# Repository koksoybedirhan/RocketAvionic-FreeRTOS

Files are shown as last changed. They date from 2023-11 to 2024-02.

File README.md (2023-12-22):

This repository contains the hardware and software of the project named "Orta İrtifa Roketler İçin FreeRTOS Tabanlı STM32 İşlemcili Aviyonik Kart Yazılım Tasarımı", which is entitled to be supported by TÜBİTAK 2209-A.

Main Avionic Components:
<br>
STM32F030C8T6, LORA RA-02, L86-M33 GPS, MPU6050, BMP180
<br>
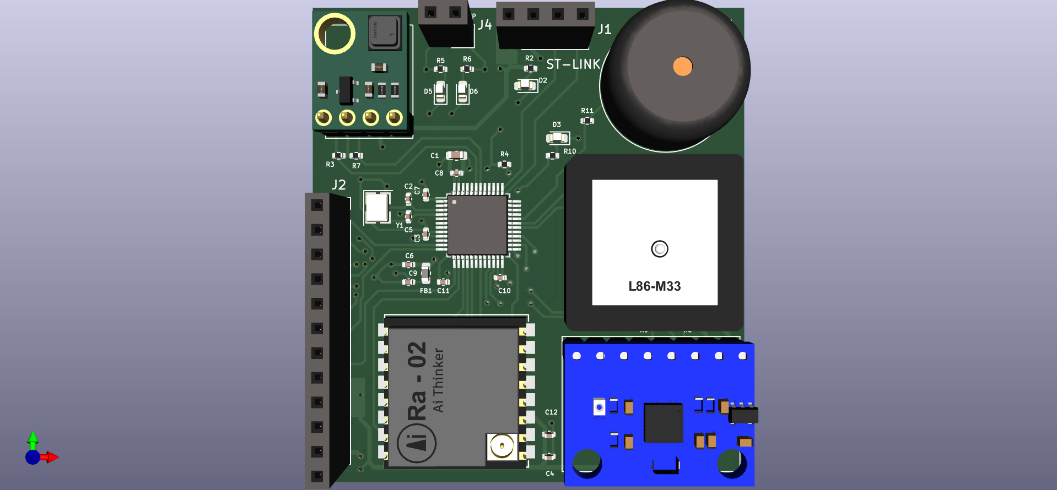
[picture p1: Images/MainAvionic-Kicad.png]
Main Avionic


Ground Station Components:
<br>
STM32F030F4P6, LORA RA-02
<br>
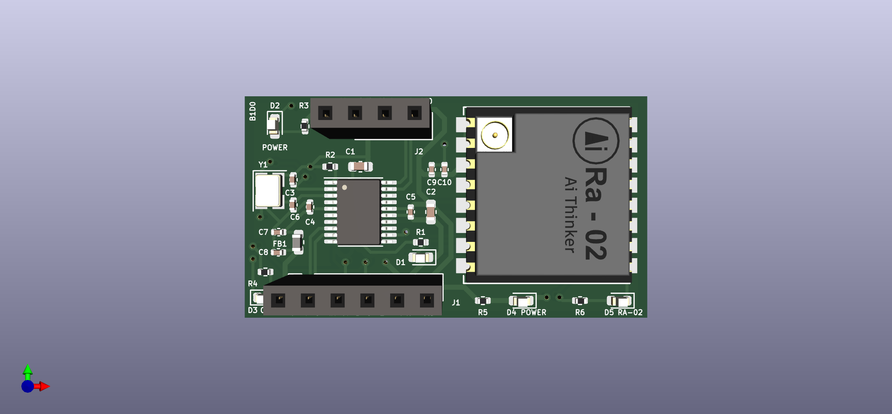
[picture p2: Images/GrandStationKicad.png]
Ground Station


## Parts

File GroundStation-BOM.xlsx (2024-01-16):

Ürün Adı | Birim Fiyatı | Adet | Link
C1, ,"1","100n","C","Capacitor_SMD:C_0603_1608Metric","Unpolarized capacitor","" | 0,16052 ₺ + KDV | 3 | https://ozdisan.com/pasif-komponentler/kapasitorler/smt-smd-ve-mlcc-kapasitorler/CL10B104KB8NNNC/9739
C2, ,"1","10u","C","Capacitor_SMD:C_0603_1608Metric","Unpolarized capacitor","" | 0,41150 ₺ + KDV | 3 | https://ozdisan.com/pasif-komponentler/kapasitorler/smt-smd-ve-mlcc-kapasitorler/CL10A106MQ8NNNC/350721
C3, C6, ,"2","10p","C","Capacitor_SMD:C_0402_1005Metric","Unpolarized capacitor","" | 0,27797 ₺ + KDV | 6 | https://ozdisan.com/pasif-komponentler/kapasitorler/smt-smd-ve-mlcc-kapasitorler/GRT1555C1H100JA02D/859838
C4, ,"1","10n","C","Capacitor_SMD:C_0402_1005Metric","Unpolarized capacitor","" | 0,10179 ₺ + KDV | 3 | https://ozdisan.com/pasif-komponentler/kapasitorler/smt-smd-ve-mlcc-kapasitorler/CL05B103KB5NNNC/30282
C5, ,"1","100n","C","Capacitor_SMD:C_0402_1005Metric","Unpolarized capacitor","" | 0,08222 ₺ + KDV | 3 | https://ozdisan.com/pasif-komponentler/kapasitorler/smt-smd-ve-mlcc-kapasitorler/CL05B104KO5NNNC/336698
C7, C8, ,"2","1u","C","Capacitor_SMD:C_0402_1005Metric","Unpolarized capacitor","" | 0,15269 ₺ + KDV | 6 | https://ozdisan.com/pasif-komponentler/kapasitorler/smt-smd-ve-mlcc-kapasitorler/CC0402KRX5R6BB105/748905
C9, ,"1","22u","C","Capacitor_SMD:C_0402_1005Metric","Unpolarized capacitor","" | 0,20750 ₺ + KDV | 3 | https://ozdisan.com/pasif-komponentler/kapasitorler/smt-smd-ve-mlcc-kapasitorler/CL05A225MQ5NNNC/521876
C10, ,"1","0.1u","C","Capacitor_SMD:C_0402_1005Metric","Unpolarized capacitor","" | 0,08222 ₺ + KDV | 3 | https://ozdisan.com/pasif-komponentler/kapasitorler/smt-smd-ve-mlcc-kapasitorler/CL05B104KO5NNNC/336698
D1, D2, D3, D4, D5, ,"5","LED","LED","LED_SMD:LED_0603_1608Metric","Light emitting diode","" | 1,08386 ₺ + KDV | 18 | https://ozdisan.com/led-ve-aydinlatma-cozumleri/led-komponentler/sinyal-ledler-renkli/19-213USRCS259TR8/645416
FB1, ,"1","120R","FerriteBead","Inductor_SMD:L_0603_1608Metric","Ferrite bead","" | 0,55479 ₺ + KDV | 3 | https://ozdisan.com/pasif-komponentler/induktorler/bead-feritler/LCB1608-101Y-N/487982
J1, ,"1","Conn_01x06_Female","Conn_01x06_Female","Connector_PinSocket_2.54mm:PinSocket_ 1x06_P2.54mm_Vertical","Generic connector, single row, 01x06, script generated (kicad-library-utils/schlib/autogen/connector/)","" | 2,04647 ₺ + KDV | 3 | https://ozdisan.com/konnektor-ve-baglanti-elemanlari/header-konnektorler/disi-headerlar/KLS1-208-1-06-S/457431
J2, ,"1","Conn_01x04_Female","Conn_01x04_Female","Connector_PinSocket_2.54mm:PinSocket_ 1x04_P2.54mm_Vertical","Generic connector, single row, 01x04, script generated (kicad-library-utils/schlib/autogen/connector/)","" | 2,89151 ₺ + KDV | 3 | https://ozdisan.com/konnektor-ve-baglanti-elemanlari/header-konnektorler/disi-headerlar/5PS1SDA85-104G0NNNAL-00/354016
R1, R3, R4, R5, R6, ,"5","330R","R","Resistor_SMD:R_0402_1005Metric","Resistor","" | 0,23099 ₺ + KDV | 15 | https://ozdisan.com/pasif-komponentler/direncler/smt-smd-ve-cip-direncler/CRCW0402330RFKTDBC/712011
R2, ,"1","10K","R","Resistor_SMD:R_0402_1005Metric","Resistor","" | 0,02033 ₺ + KDV | 3 | https://ozdisan.com/pasif-komponentler/direncler/smt-smd-ve-cip-direncler/0402WGJ0103TCE/362331
U1, ,"1","Ai-Thinker-Ra-02","Ai-Thinker-Ra-02","RF_Module:Ai-Thinker-Ra-01-LoRa","Ai-Thinker Ra- 02 410-525 MHz LoRa Module, SPI interface, U.FL antenna connector","" | 274,95 TL | 2 | https://www.robotistan.com/ra02-lora-modulu-antenli
U2, ,"1","STM32F030F4Px","STM32F030F4Px","Package_SO:TSSOP-20_4.4x6.5mm_P0.65mm","ARM Cortex-M0 MCU, 16KB flash, 4KB RAM, 48MHz, 2.4-3.6V, 15 GPIO, TSSOP-20","" | 45,20035 ₺ +KDV | 3 | https://ozdisan.com/entegre-devreler-icler/embedded-entegreler/mikroislemciler/STM32F030F4P6TR/491377
Y1, ,"1","16MHz","Crystal_GND24","Crystal:Crystal_SMD_3225-4Pin_3.2x2.5mm","Four pin crystal, GND on pins 2 and 4","" | 55,54744 ₺ + KDV | 3 | https://ozdisan.com/pasif-komponentler/kristaller-osilatorler-ve-rezanatorler/kristaller/ABM8AIG-25-000MHZ-12-2Z-/630348

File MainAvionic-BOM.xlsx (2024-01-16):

Ürün Adı | Birim Fiyatı | Adet | Link
BZ1, ,"1","Buzzer","Buzzer","Buzzer_Beeper:Buzzer_ 15x7.5RM7.6","Buzzer, polarized","" | 12,54210 ₺ + KDV | 3 | https://ozdisan.com/elektromekanik-komponentler/ses-urunleri/buzzerlar/YX-YT12075-YT03D/483098
C1, ,"1","10u","C","Capacitor_SMD:C_0603_1608Metric","Unpolarized capacitor","" | 0,41189 ₺ + KDV | 3 | https://ozdisan.com/pasif-komponentler/kapasitorler/smt-smd-ve-mlcc-kapasitorler/CL10A106MQ8NNNC/350721
C2, C5, ,"2","10p","C","Capacitor_SMD:C_0402_1005Metric","Unpolarized capacitor","" | 0,27431 ₺ + KDV | 6 | https://ozdisan.com/pasif-komponentler/kapasitorler/smt-smd-ve-mlcc-kapasitorler/GRT1555C1H100JA02D/859838
C3, ,"1","10n","C","Capacitor_SMD:C_0402_1005Metric","Unpolarized capacitor","" | 0,10189 ₺ + KDV | 3 | https://ozdisan.com/pasif-komponentler/kapasitorler/smt-smd-ve-mlcc-kapasitorler/CL05B103KB5NNNC/30282
C4, ,"1","22u","C","Capacitor_SMD:C_0402_1005Metric","Unpolarized capacitor","" | 0,20769 ₺ + KDV | 3 | https://ozdisan.com/pasif-komponentler/kapasitorler/smt-smd-ve-mlcc-kapasitorler/CL05B103KB5NNNC/30282
C6, C9, ,"2","1u","C","Capacitor_SMD:C_0402_1005Metric","Unpolarized capacitor","" | 0,15283 ₺ + KDV | 6 | https://ozdisan.com/pasif-komponentler/kapasitorler/smt-smd-ve-mlcc-kapasitorler/CC0402KRX5R6BB105/748905
C7, C8, C10, C11, ,"4","100n","C","Capacitor_SMD:C_0402_1005Metric","Unpolarized capacitor","" | 0,08229 ₺ + KDV | 12 | https://ozdisan.com/pasif-komponentler/kapasitorler/smt-smd-ve-mlcc-kapasitorler/CL05B104KO5NNNC/336698
C12, ,"1","0.1u","C","Capacitor_SMD:C_0402_1005Metric","Unpolarized capacitor","" | 0,08229 ₺ + KDV | 3 | https://ozdisan.com/pasif-komponentler/kapasitorler/smt-smd-ve-mlcc-kapasitorler/CL05B104KO5NNNC/336698
D2, D3, D5, D6, ,"4","LED","LED","LED_SMD:LED_0603_1608Metric","Light emitting diode","" | 1,08386 ₺ + KDV | 4 | https://ozdisan.com/led-ve-aydinlatma-cozumleri/led-komponentler/sinyal-ledler-renkli/19-213USRCS259TR8/645416
FB1, ,"1","120R","FerriteBead","Inductor_SMD:L_0603_1608Metric","Ferrite bead","" | 0,55479 ₺ + KDV | 3 | https://ozdisan.com/pasif-komponentler/induktorler/bead-feritler/LCB1608-101Y-N/487982
J1, ,"1","Conn_01x04_Female","Conn_01x04_Female","Connector_PinSocket_2.54mm:PinSocket_1x04_P2.54mm_Vertical","Generic connector, single row, 01x04, script generated (kicad-library-utils/schlib/autogen/connector/)","" | 2,89151 ₺ + KDV | 3 | https://ozdisan.com/konnektor-ve-baglanti-elemanlari/header-konnektorler/disi-headerlar/KLS1-208-1-06-S/457431
J2, ,"1","Conn_01x12_Female","Conn_01x12_Female","Connector_PinSocket_2.54mm:PinSocket_1x12_P2.54mm_Vertical","Generic connector, single row, 01x12, script generated (kicad-library-utils/schlib/autogen/connector/)","" | 7,67155 ₺ + KDV | 3 | https://ozdisan.com/konnektor-ve-baglanti-elemanlari/header-konnektorler/disi-headerlar/DS1023-1X12S22/460322
J4, ,"1","Conn_01x02_Female","Conn_01x02_Female","Connector_PinSocket_2.54mm:PinSocket_1x02_P2.54mm_Vertical","Generic connector, single row, 01x02, script generated (kicad-library-utils/schlib/autogen/connector/)","" | 1,57033 ₺ + KDV | 3 | https://ozdisan.com/konnektor-ve-baglanti-elemanlari/header-konnektorler/disi-headerlar/5PS1SDD85-102G0NNNXL-00/450838
R2, R5, R6, R10, ,"4","330R","R","Resistor_SMD:R_0402_1005Metric","Resistor","" | 0,23099 ₺ + KDV | 12 | https://ozdisan.com/pasif-komponentler/direncler/smt-smd-ve-cip-direncler/CRCW0402330RFKTDBC/712011
R3, R7, R8, R9, ,"4","1k5","R","Resistor_SMD:R_0402_1005Metric","Resistor","" | 0,05878 ₺ + KDV | 12 | https://ozdisan.com/pasif-komponentler/direncler/smt-smd-ve-cip-direncler/AC0402FR-071K5L/762346
R4, ,"1","10k","R","Resistor_SMD:R_0402_1005Metric","Resistor","" | 0,02033 ₺ + KDV | 3 | https://ozdisan.com/pasif-komponentler/direncler/smt-smd-ve-cip-direncler/0402WGJ0103TCE/362331
R11, ,"1","100R","R","Resistor_SMD:R_0402_1005Metric","Resistor","" | 0,02035 ₺ + KDV | 3 | https://ozdisan.com/pasif-komponentler/direncler/smt-smd-ve-cip-direncler/0402WGJ0101TCE/443485
U1, ,"1","STM32F030C8Tx","STM32F030C8Tx","Package_QFP:LQFP-48_7x7mm_P0.5mm","ARM Cortex-M0 MCU, 64KB flash, 8KB RAM, 48MHz, 2.4-3.6V, 39 GPIO, LQFP-48","" | 102,93099 ₺ + KDV | 3 | https://ozdisan.com/entegre-devreler-icler/embedded-entegreler/mikroislemciler/STM32F030C8T6/438100
U2, ,"1","Ai-Thinker-Ra-02","Ai-Thinker-Ra-02","RF_Module:Ai-Thinker-Ra-01-LoRa","Ai-Thinker Ra-02 410-525 MHz LoRa Module, SPI interface, U.FL antenna connector","" | 274,95 TL | 4 | https://www.robotistan.com/ra02-lora-modulu-antenli
U3, ,"1","L86-M33","L86-M33","F030C8T6:L86-M33","","" | 361,19 TL | 3 | https://www.empastore.com/l86-m33?gad_source=1
U4, ,"1","MPU6050","MPU6050","F030C8T6:MPU6050","","" | 77,72 TL | 3 | https://www.robotistan.com/mpu6050-6-eksen-ivme-ve-gyro-sensoru-6-dof-3-axis-accelerometer-and-gyros
U5, ,"1","BMP180","BMP180","F030C8T6:BMP180","","" | 24,45 TL | 3 | https://www.direnc.net/bmp180-dijital-barometrik-sensor
Y1, ,"1","16MHz","Crystal_GND24","Crystal:Crystal_SMD_3225-4Pin_3.2x2.5mm","Four pin crystal, GND on pins 2 and 4","" | 55,54744 ₺ + KDV | 3 | https://ozdisan.com/pasif-komponentler/kristaller-osilatorler-ve-rezanatorler/kristaller/ABM8AIG-25-000MHZ-12-2Z-/630348

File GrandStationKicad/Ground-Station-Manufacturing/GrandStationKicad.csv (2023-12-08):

Source: | C:\Users\Lenovo\Desktop\Bedirhan\TUBITAK\RocketAvionic-FreeRTOS\GrandStationKicad\GrandStationKicad.kicad_sch
Date: | Sat Dec 9 00:15:10 2023
Tool: | Eeschema (6.0.6)
Generator: | C:\Program Files\KiCad\6.0\bin\scripting\plugins/bom_csv_grouped_by_value_with_fp.py
Component Count: | 27
Ref | Qnty | Value | Cmp name | Footprint | Description | Vendor
C1, | 1 | 100n | C | Capacitor_SMD:C_0603_1608Metric | Unpolarized capacitor
C2, | 1 | 10u | C | Capacitor_SMD:C_0603_1608Metric | Unpolarized capacitor
C3, C6, | 2 | 10p | C | Capacitor_SMD:C_0402_1005Metric | Unpolarized capacitor
C4, | 1 | 10n | C | Capacitor_SMD:C_0402_1005Metric | Unpolarized capacitor
C5, | 1 | 100n | C | Capacitor_SMD:C_0402_1005Metric | Unpolarized capacitor
C7, C8, | 2 | 1u | C | Capacitor_SMD:C_0402_1005Metric | Unpolarized capacitor
C9, | 1 | 22u | C | Capacitor_SMD:C_0402_1005Metric | Unpolarized capacitor
C10, | 1 | 0.1u | C | Capacitor_SMD:C_0402_1005Metric | Unpolarized capacitor
D1, D2, D3, D4, D5, | 5 | LED | LED | LED_SMD:LED_0603_1608Metric | Light emitting diode
FB1, | 1 | 120R | FerriteBead | Inductor_SMD:L_0603_1608Metric | Ferrite bead
J1, | 1 | Conn_01x06_Female | Conn_01x06_Female | Connector_PinSocket_2.54mm:PinSocket_1x06_P2.54mm_Vertical | Generic connector, single row, 01x06, script generated (kicad-library-utils/schlib/autogen/connector/)
J2, | 1 | Conn_01x04_Female | Conn_01x04_Female | Connector_PinSocket_2.54mm:PinSocket_1x04_P2.54mm_Vertical | Generic connector, single row, 01x04, script generated (kicad-library-utils/schlib/autogen/connector/)
R1, R3, R4, R5, R6, | 5 | 330R | R | Resistor_SMD:R_0402_1005Metric | Resistor
R2, | 1 | R | R | Resistor_SMD:R_0402_1005Metric | Resistor
U1, | 1 | Ai-Thinker-Ra-02 | Ai-Thinker-Ra-02 | RF_Module:Ai-Thinker-Ra-01-LoRa | Ai-Thinker Ra-02 410-525 MHz LoRa Module, SPI interface, U.FL antenna connector
U2, | 1 | STM32F030F4Px | STM32F030F4Px | Package_SO:TSSOP-20_4.4x6.5mm_P0.65mm | ARM Cortex-M0 MCU, 16KB flash, 4KB RAM, 48MHz, 2.4-3.6V, 15 GPIO, TSSOP-20
Y1, | 1 | 16MHz | Crystal_GND24 | Crystal:Crystal_SMD_3225-4Pin_3.2x2.5mm | Four pin crystal, GND on pins 2 and 4

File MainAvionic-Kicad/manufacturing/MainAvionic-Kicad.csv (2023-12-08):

Source: | C:\Users\Lenovo\Desktop\Bedirhan\TUBITAK\RocketAvionic-FreeRTOS\MainAvionic-Kicad\MainAvionic-Kicad.kicad_sch
Date: | Sat Dec 9 00:03:14 2023
Tool: | Eeschema (6.0.6)
Generator: | C:\Program Files\KiCad\6.0\bin\scripting\plugins/bom_csv_grouped_by_value_with_fp.py
Component Count: | 37
Ref | Qnty | Value | Cmp name | Footprint | Description | Vendor
BZ1, | 1 | Buzzer | Buzzer | Buzzer_Beeper:Buzzer_15x7.5RM7.6 | Buzzer, polarized
C1, | 1 | 10u | C | Capacitor_SMD:C_0603_1608Metric | Unpolarized capacitor
C2, C5, | 2 | 10p | C | Capacitor_SMD:C_0402_1005Metric | Unpolarized capacitor
C3, | 1 | 10n | C | Capacitor_SMD:C_0402_1005Metric | Unpolarized capacitor
C4, | 1 | 22u | C | Capacitor_SMD:C_0402_1005Metric | Unpolarized capacitor
C6, C9, | 2 | 1u | C | Capacitor_SMD:C_0402_1005Metric | Unpolarized capacitor
C7, C8, C10, C11, | 4 | 100n | C | Capacitor_SMD:C_0402_1005Metric | Unpolarized capacitor
C12, | 1 | 0.1u | C | Capacitor_SMD:C_0402_1005Metric | Unpolarized capacitor
D2, D3, D5, D6, | 4 | LED | LED | LED_SMD:LED_0603_1608Metric | Light emitting diode
FB1, | 1 | 120R | FerriteBead | Inductor_SMD:L_0603_1608Metric | Ferrite bead
J1, | 1 | Conn_01x04_Female | Conn_01x04_Female | Connector_PinSocket_2.54mm:PinSocket_1x04_P2.54mm_Vertical | Generic connector, single row, 01x04, script generated (kicad-library-utils/schlib/autogen/connector/)
J2, | 1 | Conn_01x12_Female | Conn_01x12_Female | Connector_PinSocket_2.54mm:PinSocket_1x12_P2.54mm_Vertical | Generic connector, single row, 01x12, script generated (kicad-library-utils/schlib/autogen/connector/)
J4, | 1 | Conn_01x02_Female | Conn_01x02_Female | Connector_PinSocket_2.54mm:PinSocket_1x02_P2.54mm_Vertical | Generic connector, single row, 01x02, script generated (kicad-library-utils/schlib/autogen/connector/)
R2, R5, R6, R10, | 4 | 330R | R | Resistor_SMD:R_0402_1005Metric | Resistor
R3, R7, R8, R9, | 4 | 1k5 | R | Resistor_SMD:R_0402_1005Metric | Resistor
R4, | 1 | 10k | R | Resistor_SMD:R_0402_1005Metric | Resistor
R11, | 1 | 100R | R | Resistor_SMD:R_0402_1005Metric | Resistor
U1, | 1 | STM32F030C8Tx | STM32F030C8Tx | Package_QFP:LQFP-48_7x7mm_P0.5mm | ARM Cortex-M0 MCU, 64KB flash, 8KB RAM, 48MHz, 2.4-3.6V, 39 GPIO, LQFP-48
U2, | 1 | Ai-Thinker-Ra-02 | Ai-Thinker-Ra-02 | RF_Module:Ai-Thinker-Ra-01-LoRa | Ai-Thinker Ra-02 410-525 MHz LoRa Module, SPI interface, U.FL antenna connector
U3, | 1 | L86-M33 | L86-M33 | F030C8T6:L86-M33
U4, | 1 | MPU6050 | MPU6050 | F030C8T6:MPU6050
U5, | 1 | BMP180 | BMP180 | F030C8T6:BMP180
Y1, | 1 | 16MHz | Crystal_GND24 | Crystal:Crystal_SMD_3225-4Pin_3.2x2.5mm | Four pin crystal, GND on pins 2 and 4

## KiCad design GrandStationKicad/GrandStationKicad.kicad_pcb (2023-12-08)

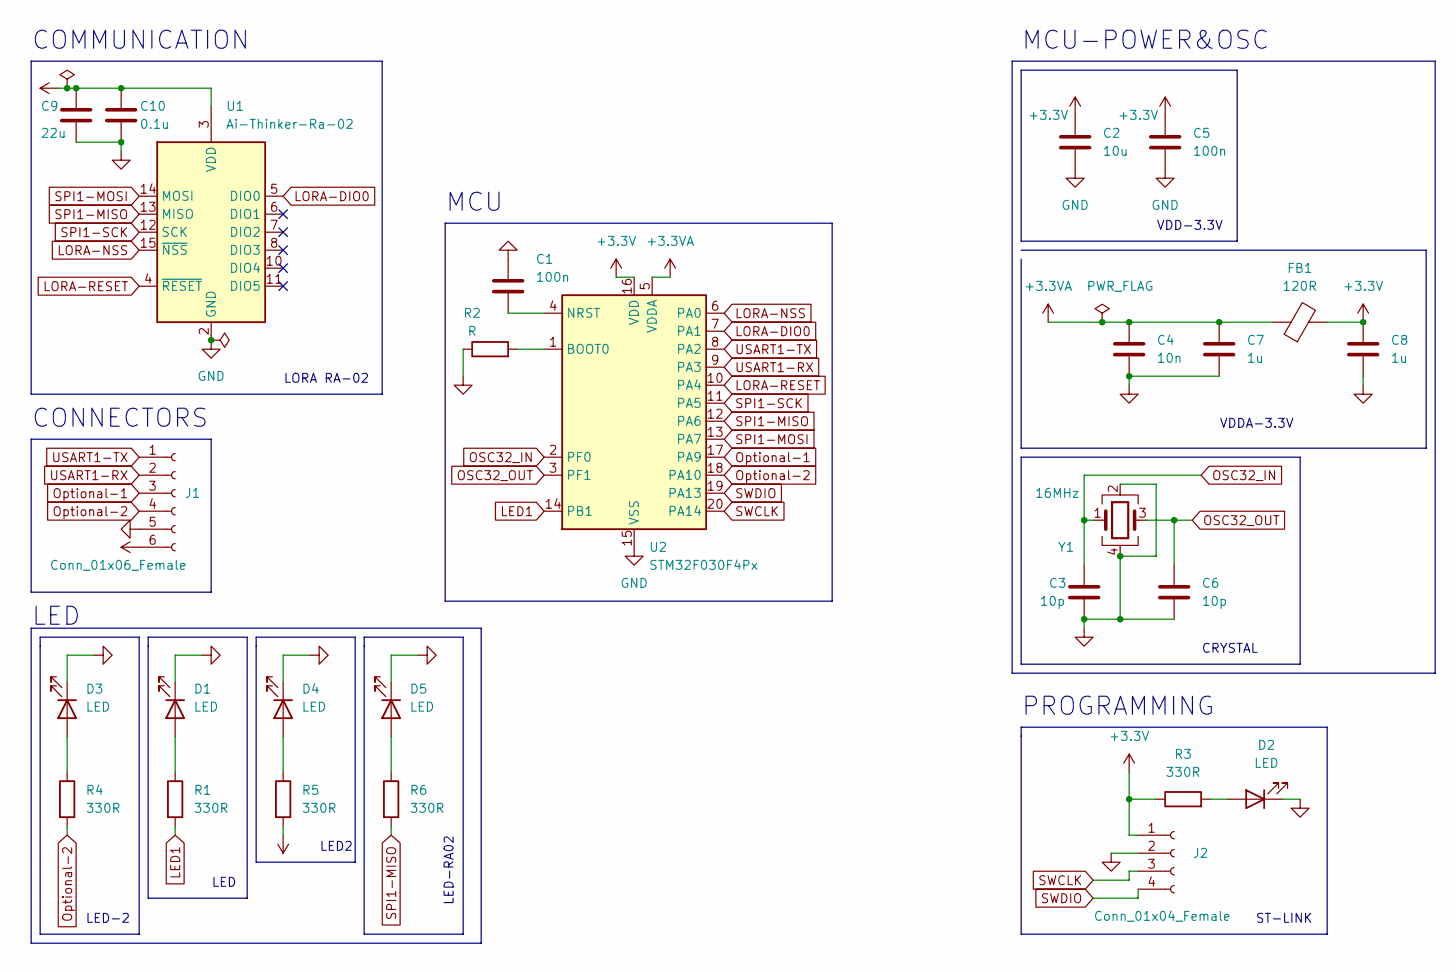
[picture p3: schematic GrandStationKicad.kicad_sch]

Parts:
C1: 100n; C_0603_1608Metric
C2: 10u; C_0603_1608Metric
C3, C6: 10p; C_0402_1005Metric
C4: 10n; C_0402_1005Metric
C5: 100n; C_0402_1005Metric
C7, C8: 1u; C_0402_1005Metric
C9: 22u; C_0402_1005Metric
C10: 0.1u; C_0402_1005Metric
D1, D2, D3, D4, D5: LED; LED_0603_1608Metric
FB1: 120R; L_0603_1608Metric
J1: Conn_01x06_Female; PinSocket_1x06_P2.54mm_Vertical
J2: Conn_01x04_Female; PinSocket_1x04_P2.54mm_Vertical
R1, R3, R4, R5, R6: 330R; R_0402_1005Metric
R2: R; R_0402_1005Metric
U1: Ai-Thinker-Ra-02; Ai-Thinker-Ra-01-LoRa
U2: STM32F030F4Px; TSSOP-20_4.4x6.5mm_P0.65mm
Y1: 16MHz; Crystal_SMD_3225-4Pin_3.2x2.5mm

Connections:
+3.3V: C2.1, C5.1, C8.1, C9.1, C10.1, FB1.2, J1.6, J2.1, R3.1, R5.2, U1.3 (VDD), U2.16 (VDD)
+3.3VA: C4.1, C7.1, FB1.1, U2.5 (VDDA)
GND: C1.1, C2.2, C3.2, C4.2, C5.2, C6.2, C7.2, C8.2, C9.2, C10.2, D1.1 (K), D2.1 (K), D3.1 (K), D4.1 (K), D5.1 (K), J1.5, J2.2, R2.1, U1.1 (GND), U1.2 (GND), U1.9 (GND), U1.16 (GND), U2.15 (VSS), Y1.2, Y1.4
LED1: R1.2, U2.14 (PB1)
LORA-DIO0: U1.5 (DIO0), U2.7 (PA1)
LORA-NSS: U1.15 (~NSS), U2.6 (PA0)
LORA-RESET: U1.4 (~RESET), U2.10 (PA4)
unnamed: C1.2, U2.4 (NRST)
unnamed: D1.2 (A), R1.1
unnamed: D2.2 (A), R3.2
unnamed: D3.2 (A), R4.1
unnamed: D4.2 (A), R5.1
unnamed: D5.2 (A), R6.1
unnamed: R2.2, U2.1 (BOOT0)
OSC32_IN: C3.1, U2.2 (PF0), Y1.1
OSC32_OUT: C6.1, U2.3 (PF1), Y1.3
Optional-1: J1.3, U2.17 (PA9)
Optional-2: J1.4, R4.2, U2.18 (PA10)
SPI1-MISO: R6.2, U1.13 (MISO), U2.12 (PA6)
SPI1-MOSI: U1.14 (MOSI), U2.13 (PA7)
SPI1-SCK: U1.12 (SCK), U2.11 (PA5)
SWCLK: J2.3, U2.20 (PA14)
SWDIO: J2.4, U2.19 (PA13)
USART1-RX: J1.2, U2.9 (PA3)
USART1-TX: J1.1, U2.8 (PA2)

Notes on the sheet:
MCU
LED
COMMUNICATION
VDDA-3.3V
PROGRAMMING
LED-RA02
CONNECTORS
LED-2
LED
VDD-3.3V
CRYSTAL
MCU-POWER&OSC
LORA RA-02
LED2
ST-LINK

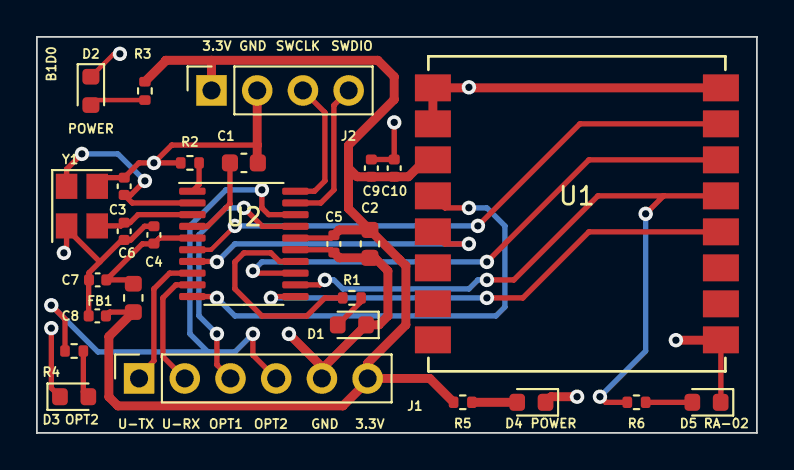
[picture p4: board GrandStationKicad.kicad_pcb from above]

Board: 2 copper layers, 40.0 x 22.0 mm, 27 parts (0 on the bottom side), 25 nets.

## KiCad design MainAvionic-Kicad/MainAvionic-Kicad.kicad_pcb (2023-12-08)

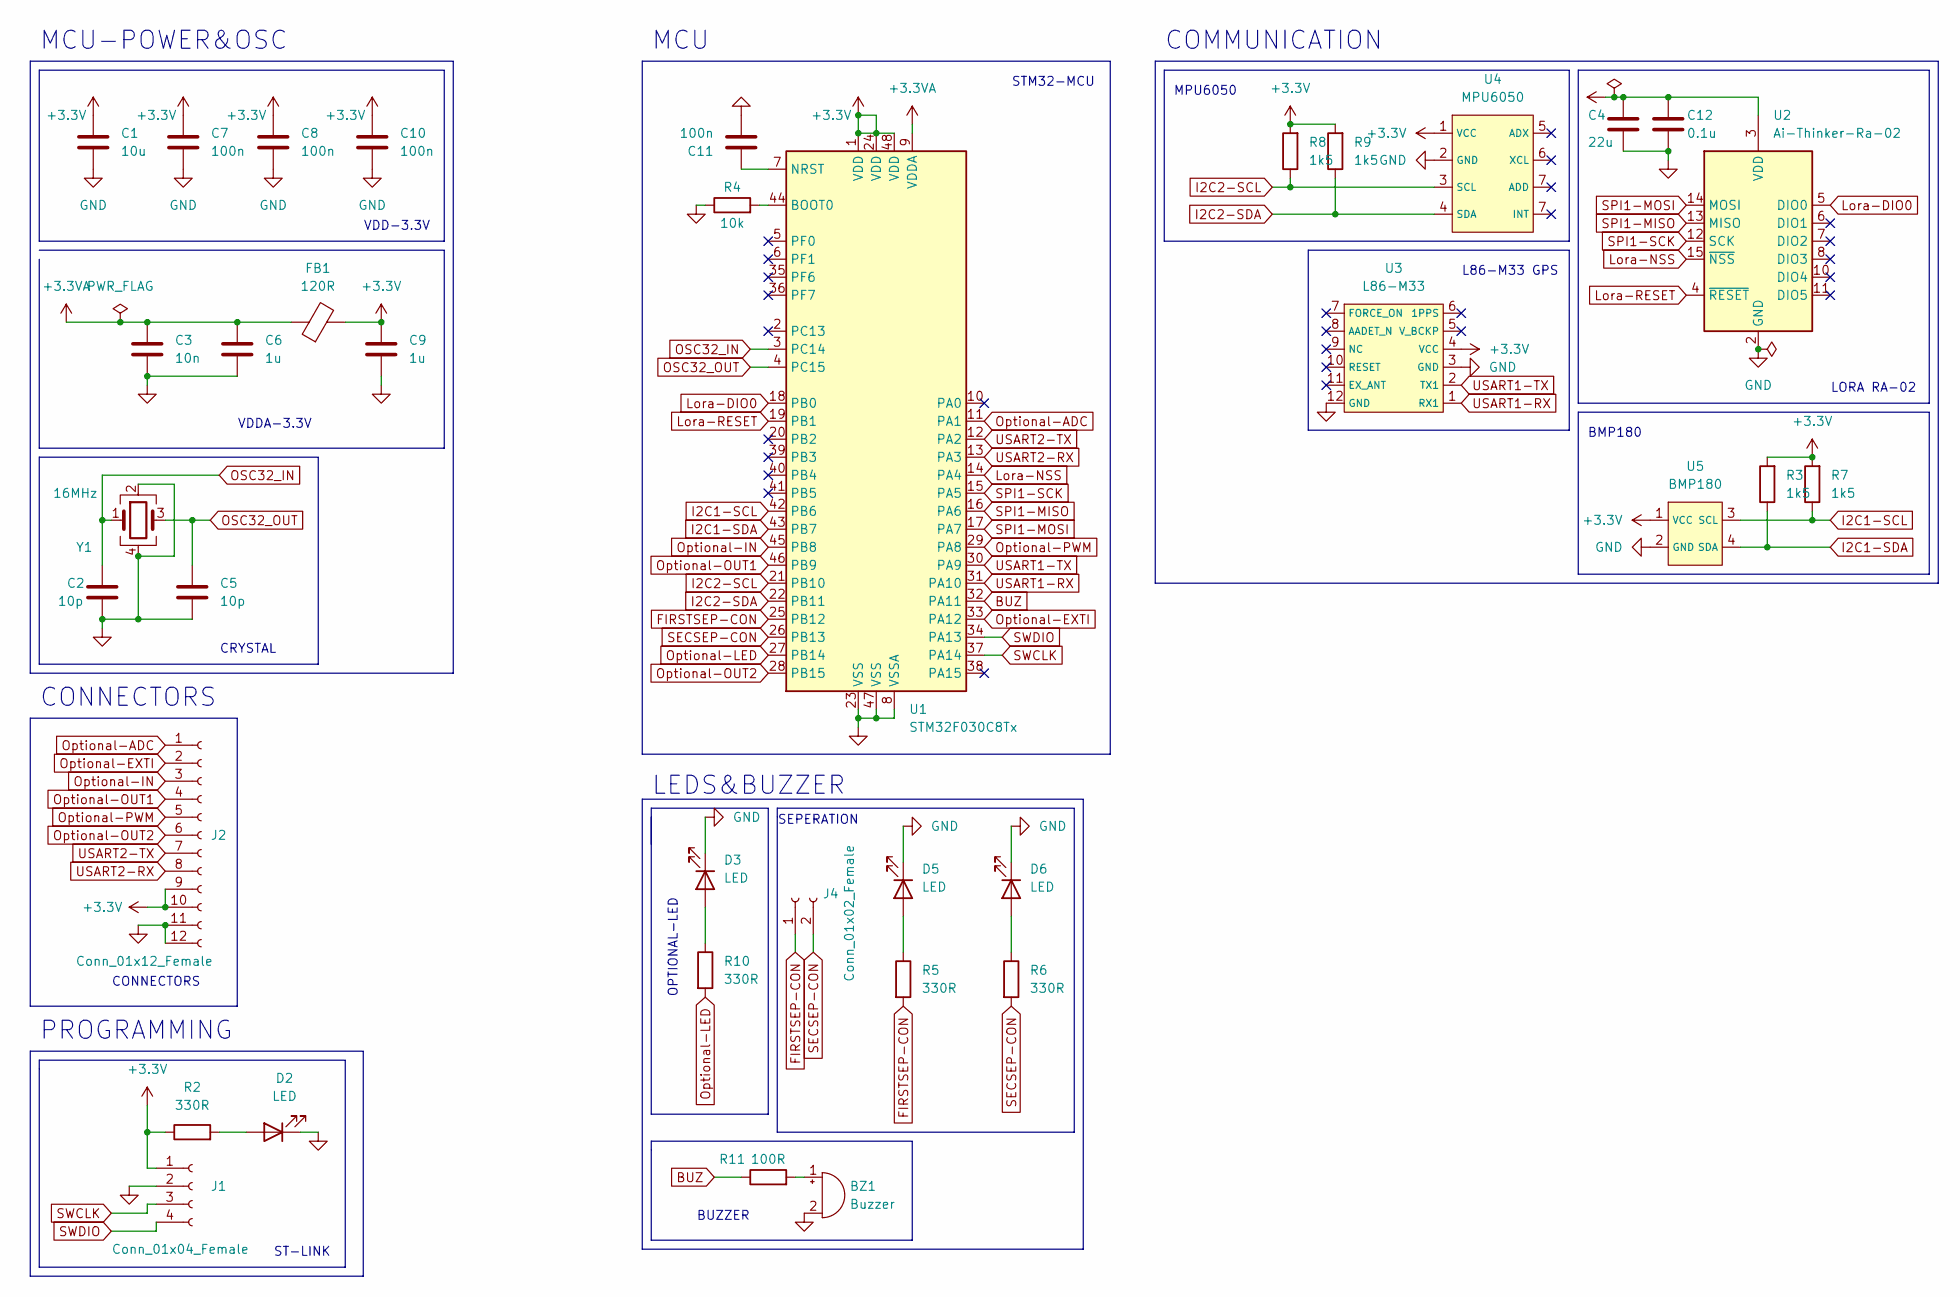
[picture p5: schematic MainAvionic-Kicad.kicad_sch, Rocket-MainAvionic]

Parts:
BZ1: Buzzer; Buzzer_15x7.5RM7.6
C1: 10u; C_0603_1608Metric
C2, C5: 10p; C_0402_1005Metric
C3: 10n; C_0402_1005Metric
C4: 22u; C_0402_1005Metric
C6, C9: 1u; C_0402_1005Metric
C7, C8, C10, C11: 100n; C_0402_1005Metric
C12: 0.1u; C_0402_1005Metric
D2, D3, D5, D6: LED; LED_0603_1608Metric
FB1: 120R; L_0603_1608Metric
J1: Conn_01x04_Female; PinSocket_1x04_P2.54mm_Vertical
J2: Conn_01x12_Female; PinSocket_1x12_P2.54mm_Vertical
J4: Conn_01x02_Female; PinSocket_1x02_P2.54mm_Vertical
R2, R5, R6, R10: 330R; R_0402_1005Metric
R3, R7, R8, R9: 1k5; R_0402_1005Metric
R4: 10k; R_0402_1005Metric
R11: 100R; R_0402_1005Metric
U1: STM32F030C8Tx; LQFP-48_7x7mm_P0.5mm
U2: Ai-Thinker-Ra-02; Ai-Thinker-Ra-01-LoRa
U3: L86-M33
U4: MPU6050
U5: BMP180
Y1: 16MHz; Crystal_SMD_3225-4Pin_3.2x2.5mm

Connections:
+3.3V: C1.1, C4.1, C7.1, C8.1, C9.1, C10.1, C12.1, FB1.2, J1.1, J2.9, J2.10, R2.1, R3.2, R7.2, R8.2, R9.2, U1.1 (VDD), U1.24 (VDD), U1.48 (VDD), U2.3 (VDD), U3.4 (VCC), U4.1 (VCC), U5.1 (VCC)
+3.3VA: C3.1, C6.1, FB1.1, U1.9 (VDDA)
BUZ: R11.1, U1.32 (PA11)
FIRSTSEP-CON: J4.1, R5.2, U1.25 (PB12)
GND: BZ1.2 (+), C1.2, C2.2, C3.2, C4.2, C5.2, C6.2, C7.2, C8.2, C9.2, C10.2, C11.2, C12.2, D2.1 (K), D3.1 (K), D5.1 (K), D6.1 (K), J1.2, J2.11, J2.12, R4.1, U1.8 (VSSA), U1.23 (VSS), U1.47 (VSS), U2.1 (GND), U2.2 (GND), U2.9 (GND), U2.16 (GND), U3.3 (GND), U3.12 (GND), U4.2 (GND), U5.2 (GND), Y1.2, Y1.4
I2C1-SCL: R7.1, U1.42 (PB6), U5.3 (SCL)
I2C1-SDA: R3.1, U1.43 (PB7), U5.4 (SDA)
I2C2-SCL: R8.1, U1.21 (PB10), U4.3 (SCL)
I2C2-SDA: R9.1, U1.22 (PB11), U4.4 (SDA)
Lora-DIO0: U1.18 (PB0), U2.5 (DIO0)
Lora-NSS: U1.14 (PA4), U2.15 (~NSS)
Lora-RESET: U1.19 (PB1), U2.4 (~RESET)
unnamed: BZ1.1 (-), R11.2
unnamed: C11.1, U1.7 (NRST)
unnamed: D2.2 (A), R2.2
unnamed: D3.2 (A), R10.1
unnamed: D5.2 (A), R5.1
unnamed: D6.2 (A), R6.1
unnamed: R4.2, U1.44 (BOOT0)
OSC32_IN: C2.1, U1.3 (PC14), Y1.1
OSC32_OUT: C5.1, U1.4 (PC15), Y1.3
Optional-ADC: J2.1, U1.11 (PA1)
Optional-EXTI: J2.2, U1.33 (PA12)
Optional-IN: J2.3, U1.45 (PB8)
Optional-LED: R10.2, U1.27 (PB14)
Optional-OUT1: J2.4, U1.46 (PB9)
Optional-OUT2: J2.6, U1.28 (PB15)
Optional-PWM: J2.5, U1.29 (PA8)
SECSEP-CON: J4.2, R6.2, U1.26 (PB13)
SPI1-MISO: U1.16 (PA6), U2.13 (MISO)
SPI1-MOSI: U1.17 (PA7), U2.14 (MOSI)
SPI1-SCK: U1.15 (PA5), U2.12 (SCK)
SWCLK: J1.3, U1.37 (PA14)
SWDIO: J1.4, U1.34 (PA13)
USART1-RX: U1.31 (PA10), U3.1 (RX1)
USART1-TX: U1.30 (PA9), U3.2 (TX1)
USART2-RX: J2.8, U1.13 (PA3)
USART2-TX: J2.7, U1.12 (PA2)

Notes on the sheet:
VDD-3.3V
STM32-MCU
LEDS&BUZZER
BUZZER
PROGRAMMING
MCU-POWER&OSC
VDDA-3.3V
CONNECTORS
CONNECTORS
COMMUNICATION
CRYSTAL
MCU
ST-LINK
SEPERATION
LORA RA-02
BMP180
MPU6050
L86-M33 GPS
OPTIONAL-LED

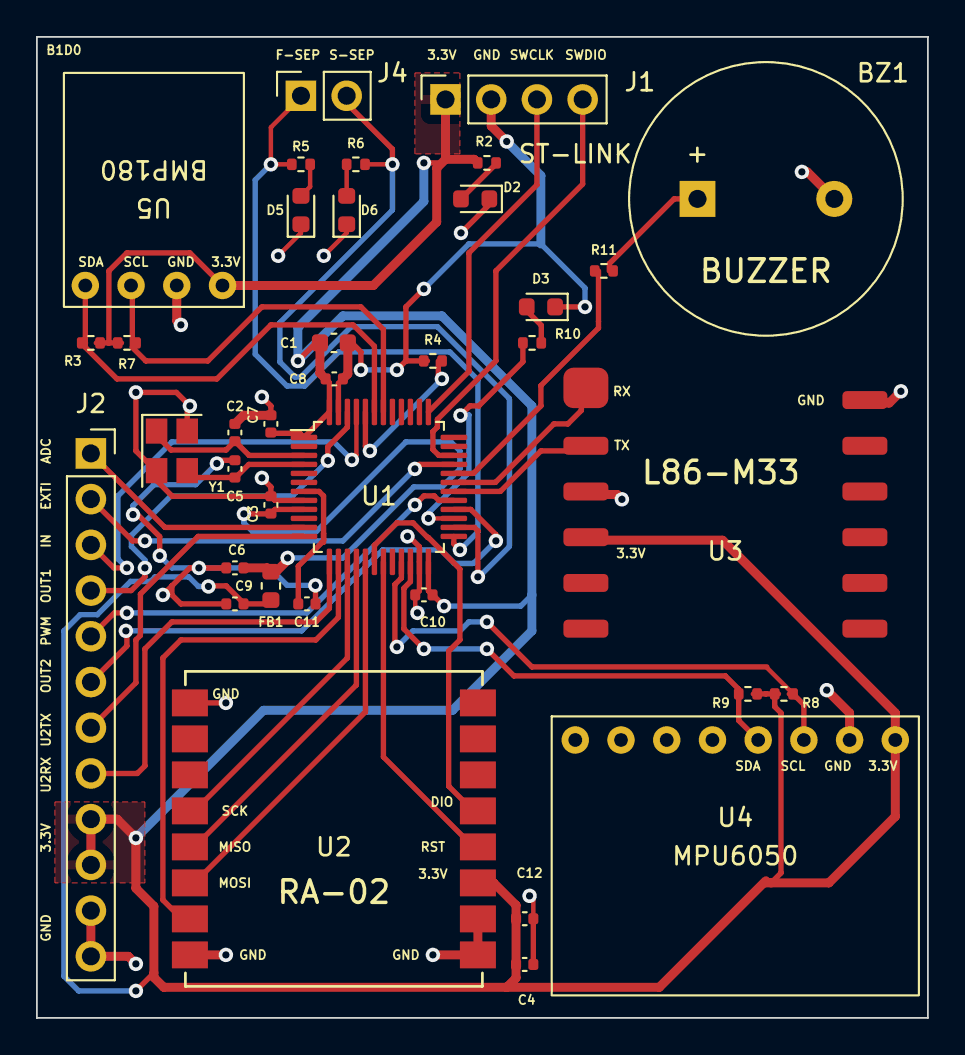
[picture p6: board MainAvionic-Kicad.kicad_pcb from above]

Board: 2 copper layers, 49.5 x 54.5 mm, 37 parts (0 on the bottom side), 38 nets.

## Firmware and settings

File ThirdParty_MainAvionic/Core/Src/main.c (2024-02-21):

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
/* Includes ------------------------------------------------------------------*/
#include "main.h"
#include "cmsis_os.h"

/* USER CODE BEGIN Includes */
#include"lwgps/lwgps.h"
#include "bme280.h"
#include "mpu6050.h"
//#include "mpu6050.c"

#include <math.h>
/* USER CODE END Includes */

I2C_HandleTypeDef hi2c1;

TIM_HandleTypeDef htim1;

UART_HandleTypeDef huart2;
UART_HandleTypeDef huart6;

osThreadId defaultTaskHandle;
osThreadId SeperationTaskHandle;
osThreadId SepSensorTaskHandle;
osThreadId GPSTaskHandle;
osThreadId CommTaskHandle;
osMutexId SimpleMutexHandle;
osSemaphoreId BinSemSepHandle;
void SystemClock_Config(void);
static void MX_GPIO_Init(void);
static void MX_I2C1_Init(void);
static void MX_USART6_UART_Init(void);
static void MX_USART2_UART_Init(void);
static void MX_TIM1_Init(void);
void StartDefaultTask(void const *argument);
void StartSeperationTask(void const *argument);
void StartSepSensorTask(void const *argument);
void StartGPSTask(void const *argument);
void StartCommTask(void const *argument);

/* USER CODE BEGIN 0 */
#define BUFFER_SIZE 25
float sensorValues[BUFFER_SIZE];
float RollAng, Altitude1, Temperature, Pressure, Humidity;
float acX, acY, acZ, gyX, gyY, gyZ, Alt, T, P, H, AltCompare;
float gpsAlt, gpsLat, gpsLong;
unsigned char buff[54];
int flag = 1;
int flagDown = 0;
int sayac = 0;
int deneme;

lwgps_t gps;
uint8_t rx_buffer[128];
uint8_t rx_index = 0;
uint8_t rx_data = 0;

typedef union {
	float sayi;
	unsigned char array[4];
} float32toInt8;

void HAL_UART_RxCpltCallback(UART_HandleTypeDef *huart) {
	if (huart == &huart6) {
		if (rx_data != '\n' && rx_index < sizeof(rx_buffer)) {
			rx_buffer[rx_index++] = rx_data;
		} else {
			lwgps_process(&gps, rx_buffer, rx_index + 1);
			rx_index = 0;
			rx_data = 0;
		}
		HAL_UART_Receive_IT(&huart6, &rx_data, 1);
	}
}

//roketin aşağı gittiği anlayan verilerin doldurulduğu buffer'i sıfırlayan kod.
void initSensorBuffer() {
	for (int i = 0; i < BUFFER_SIZE; i++) {
		sensorValues[i] = 0.0f;
	}
}

//roketin aşağı indiğini anlayan kod (buffer'a veri atıp karşılaştırma yapıyor)
void processSensorValues() {
	for (int i = 0; i < BUFFER_SIZE; i += 4) {
		if (i + 24 < BUFFER_SIZE) {
			if (sensorValues[i] >= sensorValues[i + 24]) {
				flagDown = 1;
			} else {
				flagDown = 0;
			}
		}

		// Buffer'ı sıfırla
		if (i == BUFFER_SIZE - 4) {
			initSensorBuffer();
		}
	}
}

unsigned char cs() {
	int checkSum = 0;
	for (int i = 4; i < 51; i++) {
		checkSum += buff[i];
	}
	return (unsigned char) (checkSum % 256);
}

void paket(int sayac) {
	buff[0] = 0xFF; //sabit
	buff[1] = 0xFF; //sabit
	buff[2] = 0x54; //sabit
	buff[3] = 0x52; //sabit
	buff[4] = 0x01; //id = 1 kabul ettik
	buff[5] = sayac; //paket sayaci

	float32toInt8 alt_donusturme;
	alt_donusturme.sayi = Alt;
	buff[6] = alt_donusturme.array[0];
	buff[7] = alt_donusturme.array[1];
	buff[8] = alt_donusturme.array[2];
	buff[9] = alt_donusturme.array[3];

	float32toInt8 gpsAltDonusturme;
	gpsAltDonusturme.sayi = gpsAlt;
	buff[10] = gpsAltDonusturme.array[0];
	buff[11] = gpsAltDonusturme.array[1];
	buff[12] = gpsAltDonusturme.array[2];
	buff[13] = gpsAltDonusturme.array[3];

	float32toInt8 gpsLatDonusturme;
	gpsLatDonusturme.sayi = gpsLat;
	buff[14] = gpsLatDonusturme.array[0];
	buff[15] = gpsLatDonusturme.array[1];
	buff[16] = gpsLatDonusturme.array[2];
	buff[17] = gpsLatDonusturme.array[3];

	float32toInt8 gpsLongDonusturme;
	gpsLongDonusturme.sayi = gpsLong;
	buff[18] = gpsLongDonusturme.array[0];
	buff[19] = gpsLongDonusturme.array[1];
	buff[20] = gpsLongDonusturme.array[2];
	buff[21] = gpsLongDonusturme.array[3];

	float32toInt8 AccX;
	AccX.sayi = acX;
	buff[22] = AccX.array[0];
	buff[23] = AccX.array[1];
	buff[24] = AccX.array[2];
	buff[25] = AccX.array[3];

	float32toInt8 AccY;
	AccY.sayi = acY;
	buff[26] = AccY.array[0];
	buff[27] = AccY.array[1];
	buff[28] = AccY.array[2];
	buff[29] = AccY.array[3];

	float32toInt8 AccZ;
	AccZ.sayi = acZ;
	buff[30] = AccZ.array[0];
	buff[31] = AccZ.array[1];
	buff[32] = AccZ.array[2];
	buff[33] = AccZ.array[3];

	float32toInt8 GyroX;
	GyroX.sayi = gyX;
	buff[34] = GyroX.array[0];
	buff[35] = GyroX.array[1];
	buff[36] = GyroX.array[2];
	buff[37] = GyroX.array[3];

	float32toInt8 GyroY;
	GyroY.sayi = gyY;
	buff[38] = GyroY.array[0];
	buff[39] = GyroY.array[1];
	buff[40] = GyroY.array[2];
	buff[41] = GyroY.array[3];

	float32toInt8 GyroZ;
	GyroZ.sayi = gyZ;
	buff[42] = GyroZ.array[0];
	buff[43] = GyroZ.array[1];
	buff[44] = GyroZ.array[2];
	buff[45] = GyroZ.array[3];

	float32toInt8 Aci;
	Aci.sayi = RollAng;
	buff[46] = Aci.array[0];
	buff[47] = Aci.array[1];
	buff[48] = Aci.array[2];
	buff[49] = Aci.array[3];

	buff[50] = flag; //durum
	buff[51] = cs(); //check-sum
	buff[52] = 0x0D; //sabit
	buff[53] = 0x0A; //sabit
}

/* USER CODE END 0 */

/**
 * @brief  The application entry point.
 * @retval int
 */
int main(void) {
	/* MCU Configuration--------------------------------------------------------*/

	/* Reset of all peripherals, Initializes the Flash interface and the Systick. */
	HAL_Init();

	/* Configure the system clock */
	SystemClock_Config();

	/* Initialize all configured peripherals */
	MX_GPIO_Init();
	MX_I2C1_Init();
	MX_USART6_UART_Init();
	MX_USART2_UART_Init();
	MX_TIM1_Init();
	/* USER CODE BEGIN 2 */

	HAL_TIM_Base_Init(&htim1);
	MPU6050_Init();
	lwgps_init(&gps);
	HAL_UART_Receive_IT(&huart6, &rx_data, 1);
	BME280_Config(OSRS_2, OSRS_16, OSRS_1, MODE_NORMAL, T_SB_0p5, IIR_16);

	/* USER CODE END 2 */

	/* Create the mutex(es) */
	/* definition and creation of SimpleMutex */
	osMutexDef(SimpleMutex);
	SimpleMutexHandle = osMutexCreate(osMutex(SimpleMutex));

	/* USER CODE BEGIN RTOS_MUTEX */
	/* add mutexes, ... */
	/* USER CODE END RTOS_MUTEX */

	/* Create the semaphores(s) */
	/* definition and creation of BinSemSep */
	osSemaphoreDef(BinSemSep);
	BinSemSepHandle = osSemaphoreCreate(osSemaphore(BinSemSep), 1);

	/* USER CODE BEGIN RTOS_SEMAPHORES */
	/* add semaphores, ... */
	/* USER CODE END RTOS_SEMAPHORES */

	/* USER CODE BEGIN RTOS_TIMERS */
	/* start timers, add new ones, ... */
	/* USER CODE END RTOS_TIMERS */

	/* USER CODE BEGIN RTOS_QUEUES */
	/* add queues, ... */
	/* USER CODE END RTOS_QUEUES */

	/* Create the thread(s) */
	/* definition and creation of defaultTask */
	osThreadDef(defaultTask, StartDefaultTask, osPriorityIdle, 0, 128);
	defaultTaskHandle = osThreadCreate(osThread(defaultTask), NULL);

	/* definition and creation of SeperationTask */
	osThreadDef(SeperationTask, StartSeperationTask, osPriorityAboveNormal, 0,
			128);
	SeperationTaskHandle = osThreadCreate(osThread(SeperationTask), NULL);

	/* definition and creation of SepSensorTask */
	osThreadDef(SepSensorTask, StartSepSensorTask, osPriorityNormal, 0, 128);
	SepSensorTaskHandle = osThreadCreate(osThread(SepSensorTask), NULL);

	/* definition and creation of GPSTask */
	osThreadDef(GPSTask, StartGPSTask, osPriorityBelowNormal, 0, 128);
	GPSTaskHandle = osThreadCreate(osThread(GPSTask), NULL);

	/* definition and creation of CommTask */
	osThreadDef(CommTask, StartCommTask, osPriorityLow, 0, 128);
	CommTaskHandle = osThreadCreate(osThread(CommTask), NULL);

	/* USER CODE BEGIN RTOS_THREADS */
	/* add threads, ... */
	/* USER CODE END RTOS_THREADS */

	/* Start scheduler */
	osKernelStart();

	/* We should never get here as control is now taken by the scheduler */
	/* Infinite loop */
	/* USER CODE BEGIN WHILE */
	while (1) {
		/* USER CODE END WHILE */

		/* USER CODE BEGIN 3 */
	}
	/* USER CODE END 3 */
}

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
/* USER CODE BEGIN Header_StartDefaultTask */
/**
 * @brief  Function implementing the defaultTask thread.
 * @param  argument: Not used
 * @retval None
 */
/* USER CODE END Header_StartDefaultTask */
void StartDefaultTask(void const *argument) {
	/* USER CODE BEGIN 5 */
	/* Infinite loop */
	for (;;) {
		osDelay(500);
	}
	/* USER CODE END 5 */
}

/* USER CODE BEGIN Header_StartSeperationTask */
/**
 * @brief Function implementing the SeperationTask thread.
 * @param argument: Not used
 * @retval None
 */
/* USER CODE END Header_StartSeperationTask */
void StartSeperationTask(void const *argument) {
	/* USER CODE BEGIN StartSeperationTask */
	/* Infinite loop */
	for (;;) {
		osSemaphoreWait(BinSemSepHandle, osWaitForever);
		if (flag == 1) {
			osSemaphoreRelease(BinSemSepHandle);
		} else {
			if ((RollAng <= 15 || RollAng >= -15) && Alt >= 2400) {
				HAL_GPIO_WritePin(GPIOA, GPIO_PIN_10, SET);
				flag = 2;
			}
			if ((Alt <= 600 && flag == 1) && flagDown == 1) {
				flag = 3;
			} else if (Alt <= 600 && flag == 2) {
				HAL_GPIO_WritePin(GPIOA, GPIO_PIN_9, SET);
				flag = 4;
			}
		}

		osDelay(500);
	}
	/* USER CODE END StartSeperationTask */
}

/* USER CODE BEGIN Header_StartSepSensorTask */
/**
 * @brief Function implementing the SepSensorTask thread.
 * @param argument: Not used
 * @retval None
 */
/* USER CODE END Header_StartSepSensorTask */
void StartSepSensorTask(void const *argument) {
	/* USER CODE BEGIN StartSepSensorTask */
	/* Infinite loop */
	for (;;) {

		xSemaphoreTake(SimpleMutexHandle, portMAX_DELAY);

		acX = MPU6050_Kalman_Accel_X();
		acY = MPU6050_Kalman_Accel_Y();
		acZ = MPU6050_Kalman_Accel_Z();
		gyX = MPU6050_Kalman_Gyro_X();
		gyY = MPU6050_Kalman_Gyro_X();
		gyZ = MPU6050_Kalman_Gyro_X();
		RollAng = MPU6050_Kalman_Roll_Angle();
		Temperature = BME280_Temperature();
		Pressure = BME280_Pressure();
		Humidity = BME280_Humidity();
		T = BME280_Kalman_Temp(Temperature);
		P = BME280_Kalman_Press(Pressure);
		H = BME280_Kalman_Hum(Humidity);
		Altitude1 = BME280_Altitude();
		Alt = BME280_Kalman_Alt(Altitude1);

		xSemaphoreGive(SimpleMutexHandle);

		osSemaphoreWait(BinSemSepHandle, osWaitForever);

		for (int i = 0; i < BUFFER_SIZE; i++) {
			AltCompare = BME280_Kalman_Alt(Altitude1);
			sensorValues[i] = AltCompare;
		}

		// Sensör değerlerini işle
		processSensorValues();

		osSemaphoreRelease(BinSemSepHandle);

		osDelay(500);
	}
	/* USER CODE END StartSepSensorTask */
}

/* USER CODE BEGIN Header_StartGPSTask */
/**
 * @brief Function implementing the GPSTask thread.
 * @param argument: Not used
 * @retval None
 */
/* USER CODE END Header_StartGPSTask */
void StartGPSTask(void const *argument) {
	/* USER CODE BEGIN StartGPSTask */
	/* Infinite loop */
	for (;;) {
		xSemaphoreTake(SimpleMutexHandle, portMAX_DELAY);
		gpsAlt = gps.altitude;
		gpsLat = gps.latitude;
		gpsLong = gps.longitude;
		xSemaphoreGive(SimpleMutexHandle);
		osDelay(500);
	}
	/* USER CODE END StartGPSTask */
}

/* USER CODE BEGIN Header_StartCommTask */
/**
 * @brief Function implementing the CommTask thread.
 * @param argument: Not used
 * @retval None
 */
/* USER CODE END Header_StartCommTask */
void StartCommTask(void const *argument) {
	/* USER CODE BEGIN StartCommTask */
	/* Infinite loop */
	for (;;) {
		xSemaphoreTake(SimpleMutexHandle, portMAX_DELAY);
		paket(sayac);
		sayac = sayac + 1;
		HAL_UART_Transmit(&huart2, buff, 54, 500);
		xSemaphoreGive(SimpleMutexHandle);
		osDelay(500);
	}
	/* USER CODE END StartCommTask */
}

/**
 * @brief  Period elapsed callback in non blocking mode
 * @note   This function is called  when TIM2 interrupt took place, inside
 * HAL_TIM_IRQHandler(). It makes a direct call to HAL_IncTick() to increment
 * a global variable "uwTick" used as application time base.
 * @param  htim : TIM handle
 * @retval None
 */
void HAL_TIM_PeriodElapsedCallback(TIM_HandleTypeDef *htim) {
	if (htim->Instance == TIM2) {
		HAL_IncTick();
	}
}

/**
 * @brief  This function is executed in case of error occurrence.
 * @retval None
 */
void Error_Handler(void) {
	/* USER CODE BEGIN Error_Handler_Debug */
	/* User can add his own implementation to report the HAL error return state */
	__disable_irq();
	while (1) {
	}
	/* USER CODE END Error_Handler_Debug */
}

#ifdef  USE_FULL_ASSERT
/**
  * @brief  Reports the name of the source file and the source line number
  *         where the assert_param error has occurred.
  * @param  file: pointer to the source file name
  * @param  line: assert_param error line source number
  * @retval None
  */
void assert_failed(uint8_t *file, uint32_t line)
{
  /* USER CODE BEGIN 6 */
  /* User can add his own implementation to report the file name and line number,
     ex: printf("Wrong parameters value: file %s on line %d\r\n", file, line) */
  /* USER CODE END 6 */
}
#endif /* USE_FULL_ASSERT */

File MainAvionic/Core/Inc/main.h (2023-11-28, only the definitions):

#define Optional_ADC_Pin GPIO_PIN_1
#define Optional_ADC_GPIO_Port GPIOA
#define Lora_NSS_Pin GPIO_PIN_4
#define Lora_NSS_GPIO_Port GPIOA
#define Lora_DIO0_Pin GPIO_PIN_0
#define Lora_DIO0_GPIO_Port GPIOB
#define Lora_RESET_Pin GPIO_PIN_1
#define Lora_RESET_GPIO_Port GPIOB
#define First_Seperation_Pin GPIO_PIN_12
#define First_Seperation_GPIO_Port GPIOB
#define Second_Seperation_Pin GPIO_PIN_13
#define Second_Seperation_GPIO_Port GPIOB
#define Optional_LED_Pin GPIO_PIN_14
#define Optional_LED_GPIO_Port GPIOB
#define Optional_OUT2_Pin GPIO_PIN_15
#define Optional_OUT2_GPIO_Port GPIOB
#define Optional_PWM_Pin GPIO_PIN_8
#define Optional_PWM_GPIO_Port GPIOA
#define BUZZER_Pin GPIO_PIN_11
#define BUZZER_GPIO_Port GPIOA
#define Optional_EXTI_Pin GPIO_PIN_12
#define Optional_EXTI_GPIO_Port GPIOA
#define SECSEP_LED_Pin GPIO_PIN_4
#define SECSEP_LED_GPIO_Port GPIOB
#define FIRSTSEP_LED_Pin GPIO_PIN_5
#define FIRSTSEP_LED_GPIO_Port GPIOB
#define Optional_IN_Pin GPIO_PIN_8
#define Optional_IN_GPIO_Port GPIOB
#define Optional_OUT_Pin GPIO_PIN_9
#define Optional_OUT_GPIO_Port GPIOB

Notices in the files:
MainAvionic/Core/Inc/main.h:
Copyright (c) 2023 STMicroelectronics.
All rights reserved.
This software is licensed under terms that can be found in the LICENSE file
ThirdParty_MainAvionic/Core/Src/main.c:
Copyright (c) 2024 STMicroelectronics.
